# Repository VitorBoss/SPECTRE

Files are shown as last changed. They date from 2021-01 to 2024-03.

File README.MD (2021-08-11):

# Project SPECTRE
Project SPECTRE	(Speeduino PrintEd Circuit board TjeeRdiE). This is a PCB with the hardware to run speeduino on a STM32F407VE6T board from ebay. (Or a STM32 BLACK_F407VE as it is sometimes called). 

Schematics and more information on the cpu board can be found here: (https://github.com/mcauser/BLACK_F407VE)

The case with connectors can be found here: https://nl.aliexpress.com/item/32839361268.html?spm=a2g0z.12010615.8148356.7.1da330edPBhz16

Latest version is 0.5.2

A stand alone Peak and Hold injector driver board is now in a seperate repository. See: https://github.com/Tjeerdie/Peak-And-hold-Driver

## Getting Started
Take a look at the very informative manual for speeduino:
https://speeduino.com/Speeduino_manual.pdf

There is a difference for the TPS with respect to the manual. The TPS must be fed by 3.3V and not 5V like the other speeduino boards. For best performance it is better to wire all the grounds of the sensors to the GND pins and not use the PWR_GND or carchassis for this. 

How to load the firmware to the STM32 see:
https://speeduino.com/forum/viewtopic.php?f=13&t=1914&p=26572#p26572

## Board pinout

The TS Mapping column is the pin you enter in the "Local Auxillary Input Channel Configuration" when repurposing the input pins for another purpose (example: oil pressure sensor):
https://speeduino.com/forum/viewtopic.php?f=14&t=2809

| Pin# | Function | Alternative | Switch | Tuner Studio Mapping |
|-----|---|---|---|---|
| 1 | GND_PWR | | | |
| 2 | GND_PWR | | | |
| 3 | 12V_ECU | | | |
| 4 | 12V_ECU | | | |
| 5 | INJ_CH8 | | | 66 |
| 6 | INJ_CH7 | | | 67 |
| 7 | INJ_CH5 | | | 62 |
| 8 | INJ_CH6 | | | 64 |
| 9 | IDLE1-OUT | STEP_1A_OUT | JP5 | |
| 10  | BARO | | | A9 |
| 11  | Spare_2_out | Step_2B_OUT | JP6 | 71 |
| 12  | Spare_1_Out | Step_1B_OUT | JP7 | 72 |
| 13  | IGN_CH1 | | | |
| 14  | 02_2 | | | A4 |
| 15  | FAN | | | |
| 16  | IDLE2-OUT | STEP_2A_OUT | JP8 | |
| 17  | IAT | | | |
| 18  | IAT_2 | | | A0 |
| 19  | FUEL_PUMP | | | |
| 20  | CLT_2 | | | A1 |
| 21  | RS232_TX | | | |
| 22  | GND | IGN5-OUT | JP18 | |
| 23  | O2 | | | |
| 24  | INJ_CH4 | | | |
| 25  | MAP | | | |
| 26  | GND | IGN6-OUT | JP16 | |
| 27  | CLT | | | |
| 28  | INJ_CH3 | | | |
| 29  | CANH | | | |
| 30  | GND | | | |
| 31  | IGN_CH2 | | | |
| 32  | INJ_CH1 | | | |
| 33  | GND | | | |
| 34  | RS232_RX | | | |
| 35  | TPS | | | |
| 36  | IGN_CH3 | | |  24 |
| 37  | 5V | | | |
| 38  | FLEX_IN | | | |
| 39  | VR2- | | | |
| 40  | IGN_CH4 | | |  34 |
| 41  | VR2+ | | | |
| 42  | VR1- | | | |
| 43  | VR1+ | | | |
| 44  | INJ_CH2 | | | |
| 45  | CANL | | | |
| 46  | 3.3V | | | |
| 47  | BOOST-OUT | | | |
| 48  | TACHO-OUT | | | |

## Jumper settings
There are 12 jumpers on the board to set/change various hardware configurations to suit your needs. with a sharp object scratch away the default bridge and use a solder bridge between the alternative configuration pins. The pull up resitors (JP1/JP4) are briged vs non bridged and no need to skratch anything away.
| JP# | Function | Default | Alternative|
|-----|---|---|---|
| 1 | Halleffect Pullup resistor| Not Conneced  | Connected  |
| 2 | Halleffect or VR input VR1| VR | Hall |
| 3 | Halleffect or VR input VR2| Hall | VR |
| 4 | Halleffect Pullup resistor| Not Conneced  | Connected  |
| 5 | STEP_1A_out or IDLE1-OUT  | IDLE1-OUT | STEP_1A_OUT|
| 6 | Spare_2_out or Step_2B_OUT| Spare_2_out | Step_2B_OUT|
| 7 | Spare_1_Out or Step_1B_OUT| Spare_1_Out | Step_1B_OUT|
| 8 | IDLE2-OUT or STEP_2A_OUT  | IDLE2-OUT | STEP_2A_OUT|
| 10  | Tacho out voltage		  | 5V output | 12V output |
| 15  | Flex fuel or Boot0 in | Flexfuel | Boot0 |
| 16  | Ignition 6 or GND | GND | IGN6 |
| 18  | Ignition 6 or GND _ | GND | IGN7 |

## Information for assembling a V0.5.X board
Information for board assembly and choosing components.

### RS232 and bluetooth
The hardware serial port 1 is shared between bluetooth and RS232 output on the ECU connector. So that means you can only build it with the bluetooth module in place OR the max232 ic in place not both! That will break the communication. 

Dont forget to configure the bluetooth module to use 115200 bps baudrate using the HC-05/HC-06 AT commands. 

If you want your main/Tuner studio communiation to use the hardware serial port 1 (So bluetooth or RS232 on the ECU connector). Build the speeduino firmware in the arduino IDE with no "usb support" -> "None". In that case it will default to use hardware serial 1 as the communication.

If the bluetooth comms are not working and you are using a HC-05 or HC-06 module (both are 3.3v so its safe to direcly connect to the MCU). For V0.5.2 of SPECTRE [R37,R38] can be replaced by 0 ohms. For V0.5.3 [R38] can be replaced by 0 ohm. 

### Zener diodes
If you build the board with the injector driver mosfets to be BSP78 [Q10,Q11,Q13,Q14,Q18,Q19,Q20,Q21] you can leave the bzx84C39 + 1N4148 out [33,D34,D35,D36,D37,D38,D39,D40,D41,D42,D43,D44,D45,D46,D47,D48]. These are used for clamping, but the BSP78 has internal clamping. You can use other mosfets with SOT223 footprint in place of the BSP78. If these are not clamped or reptetative avalanch rated use the clamping diodes to keep them in spec.

### Vehicle Speed input
Here is a scription how to use one of the analog spare inputs (IAT_2 = ECU pin 18) as VSS input for speeduino. This can be a hall type sensor or a porximity sesnsor. it can NOT be a VR type sensor
1. Remove C2 and C4 from the board
2. On the MCU pin headers of the board connect PA0 to PA2 with a bit of solder
3. in Tuner Studio select pin 50 (PA2) for the VSS input pin.

PA0 (pin 48 in TS) can not work as VSS pin because of conflicting interrupts with the crank sensor (PE0)

## Tested on V0.5.2/V0.5.3
The following functions have been tested and confirmed to be working on a volvo B230FK redblock engine. This a 4 cylinder engine with small turbo. A VAG wasted spark coil with internal drivers is used as ignition<br/> 

VR2 input (Trigger 2) [OK]<br/> 
Halleffect trigger input (Trigger 1) [OK]<br/>
VR1 input (Trigger 1) [OK] <br/> 
Halleffect trigger input (Trigger 2) [OK]<br/>
Manifold Absolute pressure (MAP) [OK]<br/>
Injector outputs [OK]<br/>
Lambda sensor (O2) [OK]<br/>
Throttle position input [OK]<br/>
Bluetooth module (PA9,PA10) [OK]<br/>
Battery voltage reading [OK]<br/> 
Ignition outputs [OK]<br/> 
Fuel pump relay [OK]<br/>
FAN relay [OK]<br/>
PWM idle output [OK]<br/>
Coolant temperature (CLT) [OK]<br/>
Inlet Air Temperature (IAT) [OK]<br/>
RS232 TX [OK]<br/>
RS232 RX [OK]<br/>
BOOST output [OK]<br/>
Stepper idle output [OK]<br/> 
TACHO out [OK]<br/>

## To be tested on V0.5.2/V0.5.3
BARO <br/>
CAN bus TX<br/>
CAN bus RX<br/>
FLEX fuel input<br/>
Coolant temperature (CLT_2) <br/>
Inlet Air Temperature (IAT_2) <br/>
Lambda sensor (O2_2) <br/>

## License
This project is licensed under the GNU GENERAL PUBLIC LICENSE - see the [LICENSE.md](LICENSE.md) file for details

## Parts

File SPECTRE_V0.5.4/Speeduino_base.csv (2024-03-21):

Source: | C:\Users\boss_\Github\SPECTRE\SPECTRE_V0.5.4\Speeduino_base.sch
Date: | 17/05/2022 21:27:48
Tool: | Eeschema (6.0.2)
Generator: | C:\Program Files\KiCad\bin\scripting\plugins/bom_csv_grouped_by_value.py
Component Count: | 197
Individual Components:
Item | Qty | Reference(s) | Value | LibPart | Footprint | Datasheet
 |  | A1 | Pololu_Breakout_DRV8825 | Driver_Motor:Pololu_Breakout_DRV8825 | Module:Pololu_Breakout-16_15.2x20.3mm | https://www.pololu.com/product/2982
 |  | C1 | 100nf | Speeduino_base-eagle-import:CERAMIC-100NF-50V-10%-X7R(0603) | Speeduino_base:C0603
 |  | C2 | 100nf | Speeduino_base-eagle-import:CERAMIC-100NF-50V-10%-X7R(0603) | Speeduino_base:C0603
 |  | C3 | 220nf | Speeduino_base-eagle-import:CERAMIC-220NF-25V-10%-X7R(0603) | Speeduino_base:C0603
 |  | C4 | 220nf | Speeduino_base-eagle-import:CERAMIC-220NF-25V-10%-X7R(0603) | Speeduino_base:C0603
 |  | C5 | 1nf | Speeduino_base-eagle-import:CERAMIC-1NF-50V-5%-C0G(0603) | Speeduino_base:C0603
 |  | C6 | 10uf | Speeduino_base-eagle-import:CERAMIC-10UF-25V-10%-X5R(1206) | Speeduino_base:C1206
 |  | C7 | 1nf | Speeduino_base-eagle-import:CERAMIC-1NF-50V-5%-C0G(0603) | Speeduino_base:C0603
 |  | C8 | 220nf | Speeduino_base-eagle-import:CERAMIC-220NF-25V-10%-X7R(0603) | Speeduino_base:C0603
 |  | C9 | 100nf | Speeduino_base-eagle-import:CERAMIC-100NF-50V-10%-X7R(0603) | Speeduino_base:C0603
 |  | C10 | 100nf | Speeduino_base-eagle-import:CERAMIC-100NF-50V-10%-X7R(0603) | Speeduino_base:C0603
 |  | C11 | 220nf | Speeduino_base-eagle-import:CERAMIC-220NF-25V-10%-X7R(0603) | Speeduino_base:C0603
 |  | C12 | 470uF 6.3V | Device:CP_Small | Capacitor_SMD:CP_Elec_6.3x7.7
 |  | C13 | 100nf | Speeduino_base-eagle-import:CERAMIC-100NF-50V-10%-X7R(0603) | Speeduino_base:C0603
 |  | C14 | 220nf | Speeduino_base-eagle-import:CERAMIC-220NF-25V-10%-X7R(0603) | Speeduino_base:C0603
 |  | C15 | 10uf | Speeduino_base-eagle-import:CERAMIC-10UF-25V-10%-X5R(1206) | Speeduino_base:C1206
 |  | C16 | 220nf | Speeduino_base-eagle-import:CERAMIC-220NF-25V-10%-X7R(0603) | Speeduino_base:C0603
 |  | C17 | 220nf | Speeduino_base-eagle-import:CERAMIC-220NF-25V-10%-X7R(0603) | Speeduino_base:C0603
 |  | C18 | 470uF 6.3V | Device:CP_Small | Capacitor_SMD:CP_Elec_6.3x7.7
 |  | C19 | 100nf | Speeduino_base-eagle-import:CERAMIC-100NF-50V-10%-X7R(0603) | Speeduino_base:C0603
 |  | C20 | 220nf | Speeduino_base-eagle-import:CERAMIC-220NF-25V-10%-X7R(0603) | Speeduino_base:C0603
 |  | C21 | 100nf | Speeduino_base-eagle-import:CERAMIC-100NF-50V-10%-X7R(0603) | Speeduino_base:C0603
 |  | C22 | 100nf | Speeduino_base-eagle-import:CERAMIC-100NF-50V-10%-X7R(0603) | Speeduino_base:C0603
 |  | C23 | 220nf | Speeduino_base-eagle-import:CERAMIC-220NF-25V-10%-X7R(0603) | Speeduino_base:C0603
 |  | C24 | 220nf | Speeduino_base-eagle-import:CERAMIC-220NF-25V-10%-X7R(0603) | Speeduino_base:C0603
 |  | C25 | 100nf | Speeduino_base-eagle-import:CERAMIC-100NF-50V-10%-X7R(0603) | Speeduino_base:C0603
 |  | C26 | 100nf | Speeduino_base-eagle-import:CERAMIC-100NF-50V-10%-X7R(0603) | Speeduino_base:C0603
 |  | C27 | 220nf | Speeduino_base-eagle-import:CERAMIC-220NF-25V-10%-X7R(0603) | Speeduino_base:C0603
 |  | C28 | 220nf | Speeduino_base-eagle-import:CERAMIC-220NF-25V-10%-X7R(0603) | Speeduino_base:C0603
 |  | C29 | 100nf | Device:C_Small | Speeduino_base:C0603 | ~
 |  | C30 | 100nf | Device:C_Small | Speeduino_base:C0603 | ~
 |  | C31 | 100nf | Device:C_Small | Speeduino_base:C0603 | ~
 |  | C32 | 100nf | Device:C_Small | Speeduino_base:C0603 | ~
 |  | D1 | BAT54S | Speeduino_base-eagle-import:BAT54S | Speeduino_base:SOT23
 |  | D2 | BAT54S | Speeduino_base-eagle-import:BAT54S | Speeduino_base:SOT23
 |  | D3 | BAT54S | Speeduino_base-eagle-import:BAT54S | Speeduino_base:SOT23
 |  | D4 | 1N4007 | Device:D_Small | Diode_SMD:D_SMA | ~
 |  | D5 | BAT54S | Speeduino_base-eagle-import:BAT54S | Speeduino_base:SOT23
 |  | D6 | Zener 3.6V | Device:D_Zener_Small | Diode_SMD:D_MiniMELF_Handsoldering | ~
 |  | D7 | BAT54S | Speeduino_base-eagle-import:BAT54S | Speeduino_base:SOT23
 |  | D8 | Zener 5.1V | Device:D_Zener_Small | Diode_SMD:D_MiniMELF_Handsoldering | ~
 |  | D9 | BAT54S | Speeduino_base-eagle-import:BAT54S | Speeduino_base:SOT23
 |  | D10 | BAT54S | Speeduino_base-eagle-import:BAT54S | Speeduino_base:SOT23
 |  | D11 | BAT54S | Speeduino_base-eagle-import:BAT54S | Speeduino_base:SOT23
 |  | D12 | BAT54S | Speeduino_base-eagle-import:BAT54S | Speeduino_base:SOT23
 |  | D13 | YEL | Speeduino_base-eagle-import:SMD-LED-CLEAR-YELLOW(0603) | Speeduino_base:LED-0603
 |  | D14 | 1N4007 | Device:D_Small | Diode_SMD:D_SMA | ~
 |  | D15 | BAT54S | Speeduino_base-eagle-import:BAT54S | Speeduino_base:SOT23
 |  | D16 | BAT54S | Speeduino_base-eagle-import:BAT54S | Speeduino_base:SOT23
 |  | D17 | BAT54S | Speeduino_base-eagle-import:BAT54S | Speeduino_base:SOT23
 |  | D18 | YEL | Speeduino_base-eagle-import:SMD-LED-CLEAR-YELLOW(0603) | Speeduino_base:LED-0603
 |  | D19 | BAT54S | Speeduino_base-eagle-import:BAT54S | Speeduino_base:SOT23
 |  | D20 | 1N4007 | Device:D_Small | Diode_SMD:D_SMA | ~
 |  | D21 | BAT54S | Speeduino_base-eagle-import:BAT54S | Speeduino_base:SOT23
 |  | D22 | BAT54S | Speeduino_base-eagle-import:BAT54S | Speeduino_base:SOT23
 |  | D23 | BAT54S | Speeduino_base-eagle-import:BAT54S | Speeduino_base:SOT23
 |  | D24 | BAT54S | Speeduino_base-eagle-import:BAT54S | Speeduino_base:SOT23
 |  | D26 | YEL | Speeduino_base-eagle-import:SMD-LED-CLEAR-YELLOW(0603) | Speeduino_base:LED-0603
 |  | D27 | YEL | Speeduino_base-eagle-import:SMD-LED-CLEAR-YELLOW(0603) | Speeduino_base:LED-0603
 |  | D28 | YEL | Speeduino_base-eagle-import:SMD-LED-CLEAR-YELLOW(0603) | Speeduino_base:LED-0603
 |  | D29 | YEL | Speeduino_base-eagle-import:SMD-LED-CLEAR-YELLOW(0603) | Speeduino_base:LED-0603
 |  | D30 | 1N4007 | Device:D_Small | Diode_SMD:D_SMA | ~
 |  | D31 | 1N4007 | Device:D_Small | Diode_SMD:D_SMA | ~
 |  | D32 | 1N4007 | Device:D_Small | Diode_SMD:D_SMA | ~
 |  | D33 | 1N4148WS | Device:D_Schottky_Small | Diode_SMD:D_SOD-323 | ~
 |  | D34 | BZX84C39 | Diode:BZX84Cxx | Diode_SMD:D_SOT-23_ANK | https://diotec.com/tl_files/diotec/files/pdf/datasheets/bzx84c2v4.pdf
 |  | D35 | 1N4148WS | Device:D_Schottky_Small | Diode_SMD:D_SOD-323 | ~
 |  | D36 | 1N4148WS | Device:D_Schottky_Small | Diode_SMD:D_SOD-323 | ~
 |  | D37 | BZX84C39 | Diode:BZX84Cxx | Diode_SMD:D_SOT-23_ANK | https://diotec.com/tl_files/diotec/files/pdf/datasheets/bzx84c2v4.pdf
 |  | D38 | BZX84C39 | Diode:BZX84Cxx | Diode_SMD:D_SOT-23_ANK | https://diotec.com/tl_files/diotec/files/pdf/datasheets/bzx84c2v4.pdf
 |  | D39 | 1N4148WS | Device:D_Schottky_Small | Diode_SMD:D_SOD-323 | ~
 |  | D40 | 1N4148WS | Device:D_Schottky_Small | Diode_SMD:D_SOD-323 | ~
 |  | D41 | BZX84C39 | Diode:BZX84Cxx | Diode_SMD:D_SOT-23_ANK | https://diotec.com/tl_files/diotec/files/pdf/datasheets/bzx84c2v4.pdf
 |  | D42 | BZX84C39 | Diode:BZX84Cxx | Diode_SMD:D_SOT-23_ANK | https://diotec.com/tl_files/diotec/files/pdf/datasheets/bzx84c2v4.pdf
 |  | D43 | 1N4148WS | Device:D_Schottky_Small | Diode_SMD:D_SOD-323 | ~
 |  | D44 | 1N4148WS | Device:D_Schottky_Small | Diode_SMD:D_SOD-323 | ~
 |  | D45 | 1N4148WS | Device:D_Schottky_Small | Diode_SMD:D_SOD-323 | ~
 |  | D46 | BZX84C39 | Diode:BZX84Cxx | Diode_SMD:D_SOT-23_ANK | https://diotec.com/tl_files/diotec/files/pdf/datasheets/bzx84c2v4.pdf
 |  | D47 | BZX84C39 | Diode:BZX84Cxx | Diode_SMD:D_SOT-23_ANK | https://diotec.com/tl_files/diotec/files/pdf/datasheets/bzx84c2v4.pdf
 |  | D48 | BZX84C39 | Diode:BZX84Cxx | Diode_SMD:D_SOT-23_ANK | https://diotec.com/tl_files/diotec/files/pdf/datasheets/bzx84c2v4.pdf
 |  | F1 | PPTC 16V2A | Speeduino_base-eagle-import:?1812L | Resistor_SMD:R_1812_4532Metric_Pad1.30x3.40mm_HandSolder
 |  | F2 | PPTC 16V2A | Speeduino_base-eagle-import:?1812L | Resistor_SMD:R_1812_4532Metric_Pad1.30x3.40mm_HandSolder
 |  | J1 | Conn_01x06_Male | Connector:Conn_01x06_Male | Connector_PinHeader_2.54mm:PinHeader_1x06_P2.54mm_Vertical | ~
 |  | J2 | Conn_02x04_Odd_Even | Connector_Generic:Conn_02x04_Odd_Even | Speeduino_base:PinHeader_2x04_P2.54mm_Vertical | ~
 |  | J3 | ProtoArea | Connector_Generic:Conn_02x24_Counter_Clockwise | Speeduino_base:Proto_area | ~
 |  | JP1 | Jumper_NO_Small | Device:Jumper_NO_Small | Jumper:SolderJumper-2_P1.3mm_Open_Pad1.0x1.5mm
 |  | JP2 | SolderJumper_3_Bridged12 | Jumper:SolderJumper_3_Bridged12 | Jumper:SolderJumper-3_P1.3mm_Bridged12_Pad1.0x1.5mm | ~
 |  | JP3 | SolderJumper_3_Bridged12 | Jumper:SolderJumper_3_Bridged12 | Jumper:SolderJumper-3_P1.3mm_Bridged12_Pad1.0x1.5mm | ~
 |  | JP4 | Jumper_NO_Small | Device:Jumper_NO_Small | Jumper:SolderJumper-2_P1.3mm_Open_Pad1.0x1.5mm
 |  | JP5 | SolderJumper_3_Bridged12 | Jumper:SolderJumper_3_Bridged12 | Jumper:SolderJumper-3_P1.3mm_Bridged12_Pad1.0x1.5mm | ~
 |  | JP6 | SolderJumper_3_Bridged12 | Jumper:SolderJumper_3_Bridged12 | Jumper:SolderJumper-3_P1.3mm_Bridged12_Pad1.0x1.5mm | ~
 |  | JP7 | SolderJumper_3_Bridged12 | Jumper:SolderJumper_3_Bridged12 | Jumper:SolderJumper-3_P1.3mm_Bridged12_Pad1.0x1.5mm | ~
 |  | JP8 | SolderJumper_3_Bridged12 | Jumper:SolderJumper_3_Bridged12 | Jumper:SolderJumper-3_P1.3mm_Bridged12_Pad1.0x1.5mm | ~
 |  | JP9 | SolderJumper_3_Bridged12 | Jumper:SolderJumper_3_Bridged12 | Jumper:SolderJumper-3_P1.3mm_Bridged12_Pad1.0x1.5mm | ~
 |  | JP10 | SolderJumper_3_Bridged12 | Jumper:SolderJumper_3_Bridged12 | Jumper:SolderJumper-3_P1.3mm_Bridged12_Pad1.0x1.5mm | ~
 |  | JP11 | PINHD-2X24 | Speeduino_base-eagle-import:PINHD-2X24 | Speeduino_base:2X24
 |  | JP12 | PINHD-2X24 | Speeduino_base-eagle-import:PINHD-2X24 | Speeduino_base:2X24
 |  | JP13 | Jumper_NC_Small | Device:Jumper_NC_Small | Jumper:SolderJumper-2_P1.3mm_Bridged_Pad1.0x1.5mm
 |  | JP14 | Jumper_NO_Small | Device:Jumper_NO_Small | Connector_PinHeader_2.54mm:PinHeader_1x02_P2.54mm_Vertical
 |  | JP15 | SolderJumper_3_Bridged12 | Jumper:SolderJumper_3_Bridged12 | Jumper:SolderJumper-3_P1.3mm_Bridged12_Pad1.0x1.5mm | ~
 |  | JP16 | SolderJumper_3_Bridged12 | Jumper:SolderJumper_3_Bridged12 | Jumper:SolderJumper-3_P1.3mm_Bridged12_Pad1.0x1.5mm | ~
 |  | JP18 | SolderJumper_3_Bridged12 | Jumper:SolderJumper_3_Bridged12 | Jumper:SolderJumper-3_P1.3mm_Bridged12_Pad1.0x1.5mm | ~
 |  | Q1 | AO3400 | Speeduino_base-eagle-import:SMD-MOSFET-N-CH-20V-2.1A-CJ2302(SOT-23) | Speeduino_base:SOT-23
 |  | Q6 | AO3400 | Speeduino_base-eagle-import:SMD-MOSFET-N-CH-20V-2.1A-CJ2302(SOT-23) | Speeduino_base:SOT-23
 |  | Q7 | AO3400 | Speeduino_base-eagle-import:SMD-MOSFET-N-CH-20V-2.1A-CJ2302(SOT-23) | Speeduino_base:SOT-23
 |  | Q10 | BSP78 | Speeduino_base-eagle-import:NMOSSOT223 | Speeduino_base:SOT223
 |  | Q11 | BSP78 | Speeduino_base-eagle-import:NMOSSOT223 | Speeduino_base:SOT223
 |  | Q12 | AO3400 | Speeduino_base-eagle-import:SMD-MOSFET-N-CH-20V-2.1A-CJ2302(SOT-23) | Speeduino_base:SOT-23
 |  | Q13 | BSP78 | Speeduino_base-eagle-import:NMOSSOT223 | Speeduino_base:SOT223
 |  | Q14 | BSP78 | Speeduino_base-eagle-import:NMOSSOT223 | Speeduino_base:SOT223
 |  | Q15 | BSP78 | Speeduino_base-eagle-import:NMOSSOT223 | Speeduino_base:SOT223
 |  | Q16 | BSP78 | Speeduino_base-eagle-import:NMOSSOT223 | Speeduino_base:SOT223
 |  | Q17 | BSP78 | Speeduino_base-eagle-import:NMOSSOT223 | Speeduino_base:SOT223
 |  | Q18 | BSP78 | Speeduino_base-eagle-import:NMOSSOT223 | Speeduino_base:SOT223
 |  | Q19 | BSP78 | Speeduino_base-eagle-import:NMOSSOT223 | Speeduino_base:SOT223
 |  | Q20 | BSP78 | Speeduino_base-eagle-import:NMOSSOT223 | Speeduino_base:SOT223
 |  | Q21 | BSP78 | Speeduino_base-eagle-import:NMOSSOT223 | Speeduino_base:SOT223
 |  | R1 | 2k49 | Speeduino_base-eagle-import:SMD-RES-470R-5%-1_10W(0603) | Speeduino_base:R0603
 |  | R2 | VARISTOR-18V | Speeduino_base-eagle-import:VARISTOR-7,5 | Varistor:RV_Disc_D12mm_W3.9mm_P7.5mm
 |  | R3 | 1k | Speeduino_base-eagle-import:SMD-RES-470R-5%-1_10W(0603) | Speeduino_base:R0603
 |  | R4 | 470R | Speeduino_base-eagle-import:SMD-RES-470R-5%-1_10W(0603) | Speeduino_base:R0603
 |  | R5 | 10k | Device:R_Small | Speeduino_base:R0603 | ~
 |  | R6 | 470R | Speeduino_base-eagle-import:SMD-RES-470R-5%-1_10W(0603) | Speeduino_base:R0603
 |  | R7 | 10R | Device:R_Small | Resistor_SMD:R_0603_1608Metric_Pad1.05x0.95mm_HandSolder | ~
 |  | R8 | 470R | Speeduino_base-eagle-import:SMD-RES-470R-5%-1_10W(0603) | Speeduino_base:R0603
 |  | R9 | 4k7 | Speeduino_base-eagle-import:SMD-RES-470R-5%-1_10W(0603) | Speeduino_base:R0603
 |  | R11 | 10k | Speeduino_base-eagle-import:SMD-RES-470R-5%-1_10W(0603) | Speeduino_base:R0603
 |  | R12 | 1k | Speeduino_base-eagle-import:SMD-RES-470R-5%-1_10W(0603) | Speeduino_base:R0603
 |  | R13 | 10k | Speeduino_base-eagle-import:SMD-RES-470R-5%-1_10W(0603) | Speeduino_base:R0603
 |  | R14 | 10k | Speeduino_base-eagle-import:SMD-RES-470R-5%-1_10W(0603) | Speeduino_base:R0603
 |  | R15 | 1k | Speeduino_base-eagle-import:SMD-RES-470R-5%-1_10W(0603) | Speeduino_base:R0603
 |  | R16 | 10k | Device:R_Small | Speeduino_base:R0603 | ~
 |  | R17 | 10R | Device:R_Small | Resistor_SMD:R_0603_1608Metric_Pad1.05x0.95mm_HandSolder | ~
 |  | R18 | 470R | Speeduino_base-eagle-import:SMD-RES-470R-5%-1_10W(0603) | Speeduino_base:R0603
 |  | R19 | 10k | Speeduino_base-eagle-import:SMD-RES-470R-5%-1_10W(0603) | Speeduino_base:R0603
 |  | R20 | 0R0 | Speeduino_base-eagle-import:SMD-RES-470R-5%-1_10W(0603) | Speeduino_base:R0603
 |  | R21 | 1k | Speeduino_base-eagle-import:SMD-RES-470R-5%-1_10W(0603) | Speeduino_base:R0603
 |  | R22 | 2k49 | Speeduino_base-eagle-import:SMD-RES-470R-5%-1_10W(0603) | Speeduino_base:R0603
 |  | R23 | 470R | Speeduino_base-eagle-import:SMD-RES-470R-5%-1_10W(0603) | Speeduino_base:R0603
 |  | R24 | 470R | Speeduino_base-eagle-import:SMD-RES-470R-5%-1_10W(0603) | Speeduino_base:R0603
 |  | R25 | 4k7 | Speeduino_base-eagle-import:SMD-RES-470R-5%-1_10W(0603) | Speeduino_base:R0603
 |  | R27 | 470R | Speeduino_base-eagle-import:SMD-RES-470R-5%-1_10W(0603) | Speeduino_base:R0603
 |  | R28 | 4k7 | Speeduino_base-eagle-import:SMD-RES-470R-5%-1_10W(0603) | Speeduino_base:R0603
 |  | R30 | 1k8 | Device:R_Small | Speeduino_base:R0603 | ~
 |  | R31 | 2k49 | Device:R_Small | Speeduino_base:R0603 | ~
 |  | R32 | 1k | Speeduino_base-eagle-import:SMD-RES-470R-5%-1_10W(0603) | Speeduino_base:R0603
 |  | R33 | 470R | Speeduino_base-eagle-import:SMD-RES-470R-5%-1_10W(0603) | Speeduino_base:R0603
 |  | R35 | 1k | Speeduino_base-eagle-import:SMD-RES-470R-5%-1_10W(0603) | Speeduino_base:R0603
 |  | R37 | 470R | Speeduino_base-eagle-import:SMD-RES-470R-5%-1_10W(0603) | Speeduino_base:R0603
 |  | R38 | 10R | Device:R_Small | Resistor_SMD:R_0603_1608Metric_Pad1.05x0.95mm_HandSolder | ~
 |  | R41 | 470R | Speeduino_base-eagle-import:SMD-RES-470R-5%-1_10W(0603) | Speeduino_base:R0603
 |  | R42 | 2k49 | Speeduino_base-eagle-import:SMD-RES-470R-5%-1_10W(0603) | Speeduino_base:R0603
 |  | R44 | 33k | Speeduino_base-eagle-import:SMD-RES-470R-5%-1_10W(0603) | Speeduino_base:R0603
 |  | R45 | 5k1 | Speeduino_base-eagle-import:SMD-RES-470R-5%-1_10W(0603) | Speeduino_base:R0603
 |  | R46 | 4k7 | Speeduino_base-eagle-import:SMD-RES-470R-5%-1_10W(0603) | Speeduino_base:R0603
 |  | R49 | 470R | Speeduino_base-eagle-import:SMD-RES-470R-5%-1_10W(0603) | Speeduino_base:R0603
 |  | R50 | 470R | Speeduino_base-eagle-import:SMD-RES-470R-5%-1_10W(0603) | Speeduino_base:R0603
 |  | R55 | 470R | Speeduino_base-eagle-import:SMD-RES-470R-5%-1_10W(0603) | Speeduino_base:R0603
 |  | R57 | 2k49 | Speeduino_base-eagle-import:SMD-RES-470R-5%-1_10W(0603) | Speeduino_base:R0603
 |  | R58 | 10R | Device:R_Small | Resistor_SMD:R_0603_1608Metric_Pad1.05x0.95mm_HandSolder | ~
 |  | R60 | 470R | Speeduino_base-eagle-import:SMD-RES-470R-5%-1_10W(0603) | Speeduino_base:R0603
 |  | R61 | 470R | Speeduino_base-eagle-import:SMD-RES-470R-5%-1_10W(0603) | Speeduino_base:R0603
 |  | R62 | 10R | Device:R_Small | Resistor_SMD:R_0603_1608Metric_Pad1.05x0.95mm_HandSolder | ~
 |  | R63 | 10R | Device:R_Small | Resistor_SMD:R_0603_1608Metric_Pad1.05x0.95mm_HandSolder | ~
 |  | R64 | 470R | Speeduino_base-eagle-import:SMD-RES-470R-5%-1_10W(0603) | Speeduino_base:R0603
 |  | R65 | 1k | Speeduino_base-eagle-import:SMD-RES-470R-5%-1_10W(0603) | Speeduino_base:R0603
 |  | R66 | 10K | Speeduino_base-eagle-import:SMD-RES-470R-5%-1_10W(0603) | Speeduino_base:R0603
 |  | R67 | 100R | Speeduino_base-eagle-import:SMD-RES-470R-5%-1_10W(0603) | Speeduino_base:R0603
 |  | R68 | 1k | Speeduino_base-eagle-import:SMD-RES-470R-5%-1_10W(0603) | Speeduino_base:R0603
 |  | R69 | 1k | Speeduino_base-eagle-import:SMD-RES-470R-5%-1_10W(0603) | Speeduino_base:R0603
 |  | R70 | 10R | Device:R_Small | Resistor_SMD:R_0603_1608Metric_Pad1.05x0.95mm_HandSolder | ~
 |  | R71 | 10R | Device:R_Small | Resistor_SMD:R_0603_1608Metric_Pad1.05x0.95mm_HandSolder | ~
 |  | R74 | 120R | Speeduino_base-eagle-import:SMD-RES-470R-5%-1_10W(0603) | Speeduino_base:R0603
 |  | R75 | 220R | Speeduino_base-eagle-import:SMD-RES-470R-5%-1_10W(0603) | Speeduino_base:R0603
 |  | R76 | 100R | Speeduino_base-eagle-import:SMD-RES-470R-5%-1_10W(0603) | Speeduino_base:R0603
 |  | R77 | 470R | Speeduino_base-eagle-import:SMD-RES-470R-5%-1_10W(0603) | Speeduino_base:R0603
 |  | R78 | 100R | Speeduino_base-eagle-import:SMD-RES-470R-5%-1_10W(0603) | Speeduino_base:R0603
 |  | R84 | 100R | Speeduino_base-eagle-import:SMD-RES-470R-5%-1_10W(0603) | Speeduino_base:R0603
 |  | R87 | 10K | Speeduino_base-eagle-import:SMD-RES-470R-5%-1_10W(0603) | Speeduino_base:R0603
 |  | RN1 | 100R | Device:R_Pack04_Split | Resistor_SMD:R_Array_Convex_4x0612 | ~
 |  | RN2 | 10K | Device:R_Pack04_Split | Resistor_SMD:R_Array_Convex_4x0612 | ~
 |  | RN3 | 100R | Device:R_Pack04_Split | Resistor_SMD:R_Array_Convex_4x0612 | ~
 |  | RN4 | 10K | Device:R_Pack04_Split | Resistor_SMD:R_Array_Convex_4x0612 | ~
 |  | RN6 | 9K1 | Device:R_Pack04_Split | Resistor_SMD:R_Array_Convex_4x0612 | ~
 |  | RN7 | 100R | Device:R_Pack04_Split | Resistor_SMD:R_Array_Convex_4x0612 | ~
 |  | RN8 | 10K | Device:R_Pack04_Split | Resistor_SMD:R_Array_Convex_4x0612 | ~
 |  | U1 | MAX9926UAEE+ | Speeduino_base-eagle-import:MAX9926UAEE+ | Speeduino_base:21-0055H_16
 |  | U2 | LM78M05_TO220 | Regulator_Linear:LM78M05_TO220 | Package_TO_SOT_THT:TO-220-3_Horizontal_TabUp | http://www.fairchildsemi.com/ds/LM/LM78M05.pdf
 |  | U3 | TL431DBZ | Reference_Voltage:TL431DBZ | Package_TO_SOT_SMD:SOT-23 | http://www.ti.com/lit/ds/symlink/tl431.pdf
 |  | U4 | molex_48pin | speeduino_lib:molex_48pin | Speeduino_base:Molex_48
 |  | U5 | TJA1050 | speeduino_lib:TJA1050 | Package_SO:SO-8_5.3x6.2mm_P1.27mm
 |  | U6 | MAX3232 | Interface_UART:MAX3232 | Package_SO:SOIC-16_4.55x10.3mm_P1.27mm | https://datasheets.maximintegrated.com/en/ds/MAX3222-MAX3241.pdf
 |  | U7 | MIC4427 | Driver_FET:MIC4427 | Package_SO:SO-8_3.9x4.9mm_P1.27mm | http://ww1.microchip.com/downloads/en/DeviceDoc/mic4426.pdf
 |  | U8 | MIC4427 | Driver_FET:MIC4427 | Package_SO:SO-8_3.9x4.9mm_P1.27mm | http://ww1.microchip.com/downloads/en/DeviceDoc/mic4426.pdf
 |  | U9 | MIC4427 | Driver_FET:MIC4427 | Package_SO:SO-8_3.9x4.9mm_P1.27mm | http://ww1.microchip.com/downloads/en/DeviceDoc/mic4426.pdf
 |  | U10 | MIC4427 | Driver_FET:MIC4427 | Package_SO:SO-8_3.9x4.9mm_P1.27mm | http://ww1.microchip.com/downloads/en/DeviceDoc/mic4426.pdf
 |  | U$1 | WIRELESS-BLUETOOTH-HC-05 | Speeduino_base-eagle-import:WIRELESS-BLUETOOTH-HC-05 | Speeduino_base:WIRELESS-BLUETOOTH-HC-05
Collated Components:
Item | Qty | Reference(s) | Value | LibPart | Footprint | Datasheet
1 | 1 | A1 | Pololu_Breakout_DRV8825 | Driver_Motor:Pololu_Breakout_DRV8825 | Module:Pololu_Breakout-16_15.2x20.3mm | https://www.pololu.com/product/2982
2 | 10 | C1, C2, C9, C10, C13, C19, C21, C22, C25, C26 | 100nf | Speeduino_base-eagle-import:CERAMIC-100NF-50V-10%-X7R(0603) | Speeduino_base:C0603
3 | 12 | C3, C4, C8, C11, C14, C16, C17, C20, C23, C24, C27, C28 | 220nf | Speeduino_base-eagle-import:CERAMIC-220NF-25V-10%-X7R(0603) | Speeduino_base:C0603
4 | 2 | C5, C7 | 1nf | Speeduino_base-eagle-import:CERAMIC-1NF-50V-5%-C0G(0603) | Speeduino_base:C0603
5 | 2 | C6, C15 | 10uf | Speeduino_base-eagle-import:CERAMIC-10UF-25V-10%-X5R(1206) | Speeduino_base:C1206

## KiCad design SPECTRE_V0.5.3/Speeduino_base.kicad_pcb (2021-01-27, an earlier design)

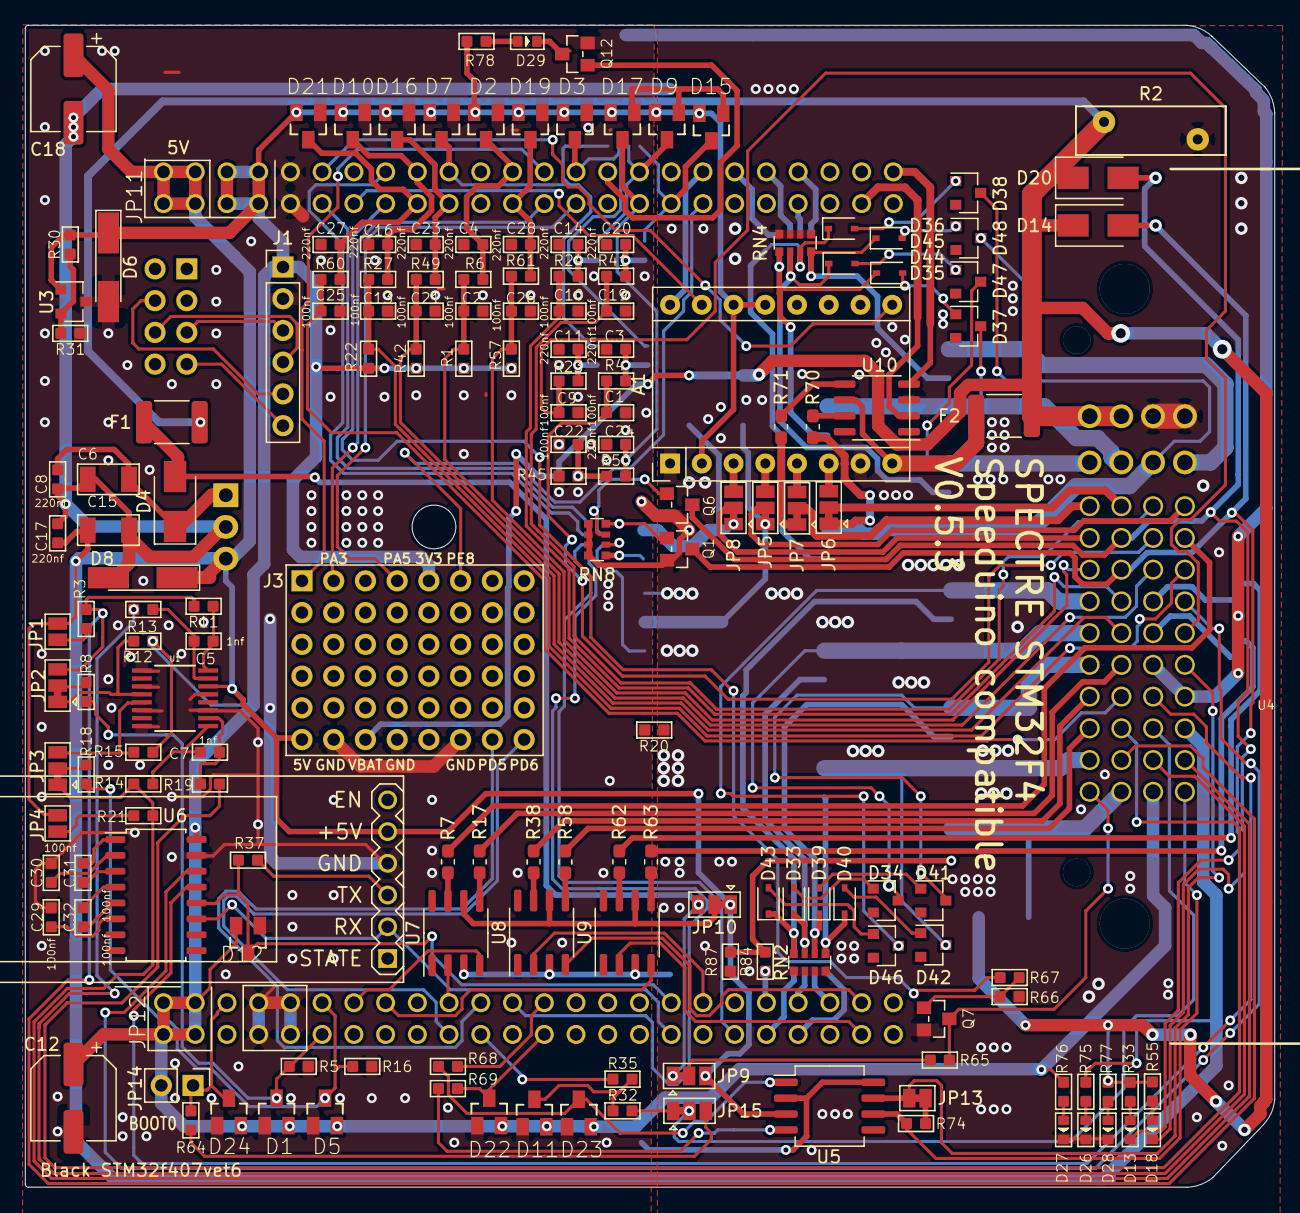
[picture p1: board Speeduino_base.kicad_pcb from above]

Board: 2 copper layers, 100.0 x 93.0 mm, 197 parts (0 on the bottom side), 180 nets.

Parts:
A1: Pololu_Breakout_DRV8825; Pololu_Breakout-16_15.2x20.3mm
C1, C2, C9, C10, C13, C19, C21, C22, C25, C26, C29, C30, C31, C32: 100nf; C0603
C3, C4, C8, C11, C14, C16, C17, C20, C23, C24, C27, C28: 220nf; C0603
C5, C7: 1nf; C0603
C6, C15: 10uf; C1206
C12, C18: 470uF 6.3V; CP_Elec_6.3x7.7
D1, D2, D3, D5, D7, D9, D10, D11, D12, D15, D16, D17, D19, D21, D22, D23, D24: BAT54S; SOT23
D4, D14, D20, D30, D31, D32: 1N4007; D_SMA
D6: Zener 3.6V; D_MiniMELF_Handsoldering
D8: Zener 5.1V; D_MiniMELF_Handsoldering
D13, D18, D26, D27, D28, D29: YEL; LED-0603
D33, D35, D36, D39, D40, D43, D44, D45: 1N4148WS; D_SOD-323
D34, D37, D38, D41, D42, D46, D47, D48: BZX84C39; D_SOT-23_ANK
F1, F2: PPTC 16V2A; R_1812_4532Metric_Pad1.30x3.40mm_HandSolder
J1: Conn_01x06_Male; PinHeader_1x06_P2.54mm_Vertical
J2: Conn_02x04_Odd_Even; PinHeader_2x04_P2.54mm_Vertical
J3: ProtoArea; Proto_area
JP1, JP4: Jumper_NO_Small; SolderJumper-2_P1.3mm_Open_Pad1.0x1.5mm
JP2, JP3, JP5, JP6, JP7, JP8, JP9, JP10, JP15, JP16, JP18: SolderJumper_3_Bridged12; SolderJumper-3_P1.3mm_Bridged12_Pad1.0x1.5mm
JP11, JP12: PINHD-2X24; 2X24
JP13: Jumper_NC_Small; SolderJumper-2_P1.3mm_Bridged_Pad1.0x1.5mm
JP14: Jumper_NO_Small; PinHeader_1x02_P2.54mm_Vertical
Q1, Q6, Q7, Q12: AO3400; SOT-23
Q10, Q11, Q13, Q14, Q15, Q16, Q17, Q18, Q19, Q20, Q21: BSP78; SOT223
R1, R22, R31, R42, R57: 2k49; R0603
R2: VARISTOR-18V; RV_Disc_D12mm_W3.9mm_P7.5mm
R3, R12, R15, R21, R32, R35, R65, R68, R69: 1k; R0603
R4, R6, R8, R18, R23, R24, R27, R33, R37, R41, R49, R50, R55, R60, R61, R64, R77: 470R; R0603
R5, R11, R13, R14, R16, R19: 10k; R0603
R7, R17, R38, R58, R62, R63, R70, R71: 10R; R_0603_1608Metric_Pad1.05x0.95mm_HandSolder
R9, R25, R28, R46: 4k7; R0603
R20: 0R0; R0603
R30: 1k8; R0603
R44: 33k; R0603
R45: 5k1; R0603
R66, R87: 10K; R0603
R67, R76, R78, R84: 100R; R0603
R74: 120R; R0603
R75: 220R; R0603
RN1, RN3, RN7: 100R; R_Array_Convex_4x0612
RN2, RN4, RN8: 10K; R_Array_Convex_4x0612
RN6: 9K1; R_Array_Convex_4x0612
U1: MAX9926UAEE+; 21-0055H_16
U2: LM78M05_TO220; TO-220-3_Horizontal_TabUp
U3: TL431DBZ; SOT-23
U4: molex_48pin; Molex_48
U5: TJA1050; SO-8_5.3x6.2mm_P1.27mm
U6: MAX3232; SOIC-16_4.55x10.3mm_P1.27mm
U7, U8, U9, U10: MIC4427; SO-8_3.9x4.9mm_P1.27mm
U$1: WIRELESS-BLUETOOTH-HC-05

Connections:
3.3V: A1.2, A1.13, A1.14, C12.1, D1.2, D2.2, D3.2, D5.2, D6.1, D7.2, D9.2, D10.2, D11.2, D12.2, D15.2, D16.2, D17.2, D19.2, D21.2, D22.2, D23.2, D24.2, J1.1, J3.5, JP11.5, JP11.6, JP11.7, JP11.8, JP12.1, JP12.2, JP12.3, JP12.4, JP14.2, R1.2, R12.2, R15.2, R22.2, R30.1, R42.2, R57.2, R76.2, R78.2, U3.1, U4.46, U6.16
5V: C15.2, C17.2, C18.1, D8.1, J3.41, JP1.2, JP4.2, JP9.3, JP10.1, JP11.1, JP11.2, JP11.3, JP11.4, R75.2, U1.14, U2.3, U4.37, U5.3, U$1.5
/BT_TX: R37.2, U$1.3
AIN_1: C2.2, R1.1, R6.1, U4.18
AIN_2: C1.2, R4.1, U4.14
AIN_3: C26.2, R57.1, R61.1, U4.20
BARO: C19.2, R41.1, U4.10
BME280_CS: J1.5, J2.4
BOOST-OUT: D30.2, Q16.2, Q16.4, U4.47
BOOT0: D24.3, JP12.5, JP14.1, R64.1
BOOT0_EXT: JP15.3, R64.2
CANH: JP13.2, U4.29, U5.7
CANL: R74.1, U4.45, U5.6
CLT: C21.2, R42.1, R49.1, U4.27
FAN: D18.-, D20.2, Q6.3, U4.15
FLEX_FUEL_IN: JP15.1, R32.2
FUEL_PUMP: D13.-, D14.2, Q1.3, U4.19
GND: C1.1, C2.1, C3.1, C4.1, C9.1, C10.1, C11.1, C12.2, C13.1, C14.1, C16.1, C19.1, C20.1, C21.1, C22.1, C23.1, C24.1, C25.1, C26.1, C27.1, C28.1, C29.2, C30.2, D1.1, D2.1, D3.1, D5.1, D6.2, D7.1, D9.1, D10.1, D11.1, D12.1, D15.1, D16.1, D17.1, D19.1, D21.1, D22.1, D23.1, D24.1, J1.2, J3.42, J3.44, J3.46, JP11.9, JP11.10, JP12.7, JP12.8, JP12.9, JP12.10, JP16.1, JP18.1, Q12.2, R5.2, R16.2, R20.1, R31.2, R45.1, RN6.1, RN6.2, RN6.3, RN6.4, U1.1, U1.3, U1.6, U1.8, U1.11, U1.13, U3.3, U4.30, U4.33, U5.2, U5.8, U6.15, U$1.4
IAT: C13.2, R22.1, R27.1, U4.17
IDLE1-OUT: D31.2, JP5.1, Q17.2, Q17.4
IDLE2-OUT: D32.2, JP8.1, Q15.2, Q15.4
IGN1-OUT: R7.1, U4.13
IGN2-OUT: R17.1, U4.31
IGN3-OUT: R38.1, U4.36
IGN4-OUT: R58.1, U4.40
IGN5-OUT: JP18.3, R62.1
IGN6-OUT: JP16.3, R63.1
INJ1-OUT: D41.1, Q13.2, Q13.4, U4.32
INJ2-OUT: D42.1, Q14.2, Q14.4, U4.44
INJ3-OUT: D34.1, Q18.2, Q18.4, U4.28
INJ4-OUT: D46.1, Q19.2, Q19.4, U4.24
INJ5-OUT: D37.1, Q10.2, Q10.4, U4.7
INJ6-OUT: D47.1, Q20.2, Q20.4, U4.8
INJ7-OUT: D38.1, Q11.2, Q11.4, U4.6
INJ8-OUT: D48.1, Q21.2, Q21.4, U4.5
MAP: C9.2, R23.1, U4.25
unnamed: C3.2, R4.2, R9.1
unnamed: C5.1, R13.2, U1.15
unnamed: C5.2, R11.2, U1.16
unnamed: C6.2, C8.2, D4.1, U2.1
unnamed: C7.1, R19.2, U1.10
unnamed: C7.2, R14.2, U1.9
unnamed: C11.2, R23.2, R25.1
unnamed: C14.2, R24.2, R28.1
unnamed: C20.2, R41.2, R46.1
unnamed: C22.2, R44.1, R45.2, R50.1
unnamed: C29.1, U6.6
unnamed: C30.1, U6.2
unnamed: C31.1, U6.1
unnamed: C31.2, U6.3
unnamed: C32.1, U6.4
unnamed: C32.2, U6.5
unnamed: D11.3, R32.1, R35.2
unnamed: D13.+, R33.1
unnamed: D18.+, R55.1
unnamed: D23.3, R68.2, U5.1
unnamed: D26.+, R75.1
unnamed: D27.+, R76.1
unnamed: D28.+, R77.1
unnamed: D29.+, R78.1
unnamed: D29.-, Q12.3
unnamed: D33.1, Q18.1, RN1.6, RN2.3
unnamed: D33.2, D34.2
unnamed: D35.1, Q10.1, RN3.8, RN4.1
unnamed: D35.2, D37.2
unnamed: D36.1, Q11.1, RN3.6, RN4.3
unnamed: D36.2, D38.2
unnamed: D39.1, Q13.1, RN1.7, RN2.2
unnamed: D39.2, D41.2
unnamed: D40.1, Q14.1, RN1.8, RN2.1
unnamed: D40.2, D42.2
unnamed: D43.1, Q19.1, RN1.5, RN2.4
unnamed: D43.2, D46.2
unnamed: D44.1, Q20.1, RN3.7, RN4.2
unnamed: D44.2, D47.2
unnamed: D45.1, Q21.1, RN3.5, RN4.4
unnamed: D45.2, D48.2
unnamed: JP1.1, R3.2
unnamed: JP2.1, R12.1, U1.4
unnamed: JP2.2, R8.2
unnamed: JP3.2, R18.2
unnamed: JP3.3, R15.1, U1.5
unnamed: JP4.1, R21.2
unnamed: JP5.2, U4.9
unnamed: JP6.2, U4.11
unnamed: JP7.2, U4.12
unnamed: JP8.2, U4.16
unnamed: JP9.2, R65.2
unnamed: JP10.2, U7.6, U8.6, U9.6
unnamed: JP13.1, R74.2
unnamed: JP15.2, U4.38
unnamed: JP16.2, U4.26
unnamed: JP18.2, U4.22
unnamed: Q1.1, RN7.1, RN8.4
unnamed: Q6.1, RN7.2, RN8.3
unnamed: Q7.1, R66.2, R67.2
unnamed: Q15.1, RN7.4, RN8.1
unnamed: Q16.1, R84.2, R87.2
unnamed: Q17.1, RN7.3, RN8.2
unnamed: R7.2, U7.7
unnamed: R17.2, U7.5
unnamed: R30.2, R31.1, U3.2
unnamed: R38.2, U8.7
unnamed: R58.2, U8.5
unnamed: R62.2, U9.7
unnamed: R63.2, U9.5
unnamed: R69.2, U5.4
unnamed: R70.2, U10.7
unnamed: R71.2, U10.5
O2: C10.2, R24.1, U4.23
PA0: C4.2, D2.3, JP11.23, R6.2
PA1: C28.2, D19.3, JP11.24, R61.2
PA2: J3.1, JP11.25
PA3: J3.2, JP11.26
PA4: D3.3, JP11.27, R9.2, RN6.7
PA5: J3.4, JP11.28
PA6: JP11.29, Q12.1
PA8: JP12.35, U8.2
PA9: JP12.34, U6.11, U$1.2
PA10: D12.3, JP12.33, R37.1, U6.12
PB1: D15.3, JP11.34, R46.2, RN6.5
PB7: JP12.15, U9.4
PB9: JP12.13, U7.4
PB12: JP11.46, U10.2
PB13: JP11.47, U10.4
PC0: C16.2, D10.3, JP11.17, R27.2
PC1: C27.2, D21.3, JP11.18, R60.2
PC2: D7.3, JP11.19, R25.2, RN6.8
PC3: C23.2, D16.3, JP11.20, R49.2
PC4: D9.3, JP11.31, R28.2, RN6.6
PC5: C24.2, D17.3, JP11.32, R50.2
PC6: JP12.39, R84.1
PC7: JP12.38, RN7.6
PC13: JP11.16, R67.1
PD0: D22.3, JP12.26, R69.1
PD1: JP12.25, R68.1
PD3: JP12.23, RN7.5
PD4: JP12.22, R35.1
PD5: J3.47, JP12.21
PD6: J3.48, JP12.20
PD7: JP12.19, U7.2
PD9: JP12.46, U9.2
PD10: JP12.45, U8.4
PD12: JP12.43, RN1.2
PD13: JP12.42, RN1.1
PD14: JP12.41, RN1.3
PD15: JP12.40, RN1.4
PE0: D1.3, JP12.12, R5.1, R8.1
PE1: D5.3, JP12.11, R16.1, R18.1
PE2: A1.9, JP11.11
PE3: JP11.12, RN7.8
PE5: A1.15, JP11.14
PE6: JP11.15, RN7.7
PE7: A1.16, JP11.35
PE8: J3.6, JP11.36
PE9: JP11.37, RN3.1
PE11: JP11.39, RN3.2
PE13: JP11.41, RN3.4
PE14: JP11.42, RN3.3
PWR_GND: A1.1, A1.7, C6.1, C8.1, C15.1, C17.1, C18.2, D8.2, D26.-, D27.-, D28.-, Q1.2, Q6.2, Q7.2, Q10.3, Q11.3, Q13.3, Q14.3, Q15.3, Q16.3, Q17.3, Q18.3, Q19.3, Q20.3, Q21.3, R2.1, R20.2, R66.1, R87.1, RN2.5, RN2.6, RN2.7, RN2.8, RN4.5, RN4.6, RN4.7, RN4.8, RN8.5, RN8.6, RN8.7, RN8.8, U2.2, U4.1, U4.2, U7.3, U8.3, U9.3, U10.3
RS232_RX: U4.34, U6.13
RS232_TX: U4.21, U6.14
SPI1_MISO: J1.6, J2.7
SPI1_MOSI: J1.4, J2.6
SPI1_SCK: J1.3, J2.5
STEP_1A_OUT: A1.4, JP5.3
STEP_1B_OUT: A1.5, JP7.3
STEP_2A_OUT: A1.3, JP8.3
STEP_2B_OUT: A1.6, JP6.3
Spare_1-Out: JP7.1, R71.1
Spare_2-Out: JP6.1, R70.1
TACHO-OUT: Q7.3, R65.1, U4.48
TPS: C25.2, R60.1, U4.35
VBAT: D14.1, D20.1, D30.1, D31.1, D32.1, F1.1, F2.1, J3.43, R2.2, R33.2, R44.2, R55.2, R77.2, U4.3, U4.4
VBAT_F1: D4.2, F1.2, JP9.1, JP10.3
VR1+: JP2.3, R3.1, R11.1, U4.43
VR1-: R13.1, U4.42
VR2+: JP3.1, R14.1, R21.1, U4.41
VR2-: R19.1, U4.39
V_IDLE: A1.8, F2.2, U10.6

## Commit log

2021-01-27 Increased VBAT width
    [Speeduino_base.kicad_pcb, Speeduino_base.sch]
2024-03-21 Minor changes
    [Speeduino_base.csv, Speeduino_base.kicad_pcb]
